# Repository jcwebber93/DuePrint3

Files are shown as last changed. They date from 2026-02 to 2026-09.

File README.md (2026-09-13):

# DuePrint3
Duet 3 to Stratasys PDB Interface Board. Used to convert a Stratasys Prodigy series printer (Dimension, uPrint, Fortus 250) to use a modern control board & firmware. This conversion is fully reversable (assuming the printer functions to begin with). Many thanks to AJ Quick and Archeantus (Jeremy) for their past efforts in detailing the electronics of the Dimension/uPrint machines, as well as sharing details on their Duet 2 WiFi conversions.
* https://wiki.cnc.xyz/Stratasys_uPrint_Retrofit
* https://forum.duet3d.com/topic/12647/another-stratasys-uprint-retrofit

[Additional details for this project on the Duet3D forums.](https://forum.duet3d.com/topic/37434/dueprint-with-a-duet-3-6hc-stratasys-dimension-conversion)

DuetPrint3 Block Diagram

IMG_4153(1)

DuePrint3 v2 5 0

At present, the implementation focuses on the Dimension 1200es printers (the implementations linked above focus on the uPrint series, which is quite similar. The electronics are laid out a touch differently, meaning the layout of the new hardware must change, as well where the stepper motor wiring taps in to the existing harness). The Duet 3 Mainboard 6HC, as well as the DP3EXB module (natively running RepRapFirmware/Duet3Expansion) interface with 17 inputs, and 11 outputs.
### Inputs
|Device|RRF Pin Name|Function|Gcode|Dependancy|Note|
|---|---|---|---|---|---|
|6HC HEADER 7|io2.in|PRINT BED TOUCH PR LIM SW|`M558 P5 H5 F1200:200 T18000 A3 C"!io2.in" ; Z probe`||Used for Z probing|
|6HC HEADER 9|io6.in|Z-AXIS EOT|`M574 Z2 S1 P"!io6.in" ; Z EOT to Z endstop on high side`||Remapped as part of Z homing routine|
|6HC HEADER 11|io4.in|Y-AXIS EOT|`M950 J6 C"!io4.in" ; Y EOT (High, Back)`||Used for Y end of travel (high side, back of printer)|
|6HC HEADER 13|io3.in|X-AXIS EOT|`M950 J5 C"!io3.in" ; X EOT (High)`||Used for X end of travel|
|6HC HEADER 15|io0.in|X-AXIS HOME SW|`M574 X1 S1 P"!io0.in" ; X home limit (low side)`||Used for X homing (low side)|
|6HC HEADER 17|io1.in|Y-AXIS HOME SW|`M574 Y1 S1 P"!io1.in" ; Y home limit (low side, front of printer)`||Used for Y homing (low side, front of printer)|
|6HC HEADER 19|io5.in|Z-AXIS HOME SW|`M950 J7 C"!io5.in" ; Z Home`||Remapped as part of Z homing routine|
|6HC HEADER 21|io8.in|POWER I/O|`M950 J11 C"io8.in" ; Power Switch Status`||Front power switch status|
|6HC HEADER 23|io7.in|PRINT HEAD TEMP ALARM|`M950 J9 C"!io7.in" ; Print Head Temp Alarm`||Print head temperature alarm|
|DP3EXB |PA07|CHAMBER TEMP ALARM|`M950 J10 C"124.pa07" ; Chamber Temp Alarm`||Chamber temperature alarm|
|DP3EXB |PA06|HEAD THERMOSTAT STATUS|`M950 J1 C"124.pa06" ; Head Thermostat`||Head thermostat|
|DP3EXB |PA05|DOOR SWITCH|`M950 J2 C"124.pa05" ; Door Status`||Door switch status|
|DP3EXB |PA04|SUPPORT TOGGLE SW|`M950 J3 C"124.pa04" ; T1 Toggle`||T1 (Support) toggle sensor|
|DP3EXB |PB11|MODEL TOGGLE SW|`M950 J4 C"124.pb08" ; T0 toggle`||T0 (Model) toggle sensor|
|6HC HEADER 18&20|temp0&VSSA|CHAMBER THERM|`M308 S0 A"Chamber" P"temp0" Y"linear-analog" F0 B-42 C113 ; Chamber Temp Sensor`||Chamber temperature sensor|
|6HC HEADER 22&24|temp2&VSSA|SUPPORT THERM|`M308 S1 A"Model" P"temp1" Y"linear-analog" F0 B12.5 C328 ; T1 (Support) Temp Sensor`||Tool 1 (Support) temperature sensor|
|6HC HEADER 26&28|temp1&VSSA|MODEL THERM|`M308 S2 A"Support" P"temp2" Y"linear-analog" F0 B12.5 C328 ; T0 (Model) Temp Sensor`||Tool 0 (Model) temperature sensor|

### Outputs
|Device|RRF Pin Name|Function|Gcode|Dependancy|Note|
|---|---|---|---|---|---|
|6HC HEADER 2|io0.out|120V ON|`M950 P5 C"io0.out" ; 120V On`|Outputs need to be enabled via "M42 P7 S0"|Enables 120V power supplies|
|6HC HEADER 3|out4|48V RTN|`M950 P7 C"!out4"  ; Disable Outputs`||This provides power to DuePrint3 level shifters.|
|6HC HEADER 4|io1.out|POWER ON|`M950 P6 C"io1.out" ; Controlled Shutdown`|Outputs need to be enabled via "M42 P7 S0"|When enabled, allows the printer to handle a controlled shutdown when front power switch is toggled|
|6HC HEADER 6|io3.out|MOTOR ENA|`M950 P1 C"io3.out" ;Extruder Motor`|Outputs need to be enabled via "M42 P7 S0"|Enables the extruder motor|
|6HC HEADER 8|io4.out|CHAMBER HEATER ENA|`M950 H0 C"io4.out" T0 ; Chamber heater, Sensor 0`|Outputs need to be enabled via "M42 P7 S0"|Chamber heater|
|6HC HEADER 10|io2.out|BLOWER ENA|`M950 P0 C"io2.out" ; Head Blower Fan`|Outputs need to be enabled via "M42 P7 S0"|Used to enable or disable head blower fan|
|6HC HEADER 12|io7.out|SUPPORT HEATER ENA|`M950 H2 C"io7.out" T2 ; T1 heater, Sensor 2`|Outputs need to be enabled via "M42 P7 S0"|Tool 1 (Support) heater|
|6HC HEADER 14|io5.out|EXTRUDER MODEL HEATER ENA|`M950 H1 C"io5.out" T1 ; T0 heater, Sensor 1`|Outputs need to be enabled via "M42 P7 S0"|Tool 0 (Model) heater|
|6HC HEADER 16|io6.out|DOOR SOLENOID ENA|`M950 P3 C"io6.out" ; Door Lock`|Outputs need to be enabled via "M42 P7 S0"|Used to enable or disable the door lock|
|DP3EXB |PA08|LED LIGHTS ENA|`M950 P4 C"124.pa24" ; Chamber Lights`||Used to enable or disable chamber lights|
|DP3EXB |PA10|PRINT BED TOUCH PR ENA|`M950 P2 C"124.pa25" ;Doesn't seem to function?`||Does not seem to have a function|

### Other
|Header Pin|Desc.|Label|
|---|---|---|
|6HC HEADER 1|N/A|NC|
|6HC HEADER 5|N/A|48V|
|6HC HEADER 25|N/A|NC|
|6HC HEADER 27|N/A|5V|
|6HC HEADER 29|N/A|GND|
|6HC HEADER 30|N/A|GND|

### Spares Header
|Header Pin|Desc.|Label|
|---|---|---|
|SPARE 1||GND|
|SPARE 2|PA27|SPR4|
|SPARE 3|PA02|SPR1|
|SPARE 4|PA23|SPR3|
|SPARE 5|PA01|SPR2|
|SPARE 6|PA19|I_SPR2|
|SPARE 7|PA12|I_SPR1|
|SPARE 8|PA17|SPR5|
|SPARE 9||5V|
|SPARE 10|PA09|SPR6|
|SPARE 11||GND|
|SPARE 12|PA11|SPR7|
|SPARE 13||12V|
|SPARE 14|PA18|SPR8|

The 6HC directly drives the X, Y, and Z stepper motors (vs. controlling them through the Stratasys PDB). The 6HC, unlike the Duet2 (and Duex boards) does not natively have STEP/DIR pins used to emit step and direction pulses. Instead, a DP3EXB expansion board running a fork of Duet3Expansion is used to natively control the extruder's closed loop DC motor. The extruder can be tuned via the ClosedLoopTuning plugin for DWC, with the motor parameters being configured in Config.g. RRF is able to monitor the motor for position errors.

## Materials
[A detailed BOM can be found here](https://github.com/jcwebber93/DuePrint3/blob/v2.5.0/DuePrint3%20BOM.xlsx), with the approximate cost being ~$660 (60% of this is Duet3D 6HC, DP3EXB Module, and DuetScreen).

## Interface Board Design
[The KidCad project for the DuePrint3 board can be found here](https://github.com/jcwebber93/DuePrint3/tree/v2.5.0/DuePrint3%20KiCad%20Project)

## Wiring
[A detailed wire list can be found here.](https://github.com/jcwebber93/DuePrint3/blob/v2.5.0/DuePrint3%20Wire%20List.xlsx) Connectors & crimps for the Duet 3 6HC are supplied with the board, but are JST VH (stepper motors) and Molex KK / Wurth WR-WTB (Wurth connectors/contacts are supplied with Duet Boards). The interface board 6HC and spares header are JST PHD, and spare 5v and 12v headers are Molex Micro-3.0 series connectors & crimps. The headers for the PBD ribbon cables are Samtec EHT series headers.

## DP3EXB Prep
DP3EXB prep to detailed

## Interface Board Prep
If the Interface Board (w/Sammy-C21) is the only CAN-FD device, aside from the Duet 3 6HC, place a 2-socket jumper on J13 as indicated to enable the CAN-FD termination resistor.



J11 connects to the 6HC. J12 can be used with additional expansion boards (such as a Duet 3 SZP on the print head, which could be used as an accelerometer or for bed scanning), provided the CAN-FD bus is terminated on the additional board.

## RepRapFirmware Prep
At present, the 6HC and DP3EXB are running a fork of 3.6.3 (to be documented). [Configuration files are located here](https://github.com/jcwebber93/DuePrint3/tree/v2.0.0/Duet%203%20Configuration/System%20Directory), and [Macros are located here.](https://github.com/jcwebber93/DuePrint3/tree/v2.0.0/Duet%203%20Configuration/Macros%20Directory)

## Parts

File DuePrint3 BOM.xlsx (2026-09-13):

 |  |  |  |  | $661.01 |  | https://www.digikey.com/short/q54m7hm0
Item | Part Number | Description | Quantity | REF | Price | EXT Price | Note | Link
1 |  | Duet 3 Mainboard 6HC | 1 |  | $269.99 | $269.99 |  | https://www.filastruder.com/collections/duet3d/products/duet-3-mainboard-6hc
2 |  | DuePrint3 v2.5.0 PCB | 1 |  | $30.00 | $30.00
3 | LRS-75-48 | Power Suppy, AC/DC, 48V 75W | 1 |  | $14.10 | $14.10 |  | https://www.digikey.com/en/products/detail/mean-well-usa-inc/LRS-75-48/7705054
4 | PAAD04010BH-0000 | Fan, 5V, 40x10, 0.25A | 2 | FAN 1, FAN 2 | $5.33 | $10.66 | The Stratasys 12V/5V PSU requires a minimum load of 0.7A on 5V, so a "dummy" load is required (else the machine fails to power on). Fans helps fill that "dummy" load. | https://www.digikey.com/en/products/detail/boyd-laconia-llc/PAAD04010BH-0000/20532210
5 | CL21B103KAANNNC | 10nF, 25V X7R Cap, 0805 | 1 | C3 | $0.10 | $0.10 |  | https://www.digikey.com/en/products/detail/samsung-electro-mechanics/CL21B103KAANNNC/3888092
6 | CL21B104KCFSFNE | 0.1 uF, 100V X7R Cap, 0805 | 2 | C1,C2 | $0.10 | $0.20 |  | https://www.digikey.com/en/products/detail/samsung-electro-mechanics/cl21b104kcfsfne/3888581
7 | 150080BS75000 | LED, Blue, 0805 | 1 | D1 (12V) | $0.19 | $0.19 |  | https://www.digikey.com/en/products/detail/w%C3%BCrth-elektronik/150080BS75000/4489912
8 | 150080VS75000 | LED, Green, 0805 | 1 | D2 (5V_SW) | $0.19 | $0.19 |  | https://www.digikey.com/en/products/detail/w%C3%BCrth-elektronik/150080VS75000/4489924
9 | 150080AS75000 | LED, Amber, 0805 | 1 | D3 (5V) | $0.25 | $0.25 |  | https://www.digikey.com/en/products/detail/w%C3%BCrth-elektronik/150080AS75000/11479384
10 | EHT-110-01-F-D | Conn, Header, 20 pos, EHT | 1 | J1 | $2.77 | $2.77 |  | https://www.digikey.com/en/products/detail/samtec-inc/EHT-110-01-F-D/6678014
11 | 436500315 | Conn, Header, 3 pos, MicroFit- 3.0 | 1 | J4 | $1.15 | $1.15 |  | https://www.digikey.com/en/products/detail/molex/0436500315/283462
12 | B14B-PHDSS | Conn, Header, 14 pos, JST PHD, 2.0 | 1 | J14 | $0.47 | $0.47 |  | https://www.digikey.com/en/products/category/rectangular-connectors/2027
13 | B30B-PHDSS | Conn, Header, 30 pos, JST PHD, 2.0 | 1 | J16 | $0.86 | $0.86 |  | https://www.digikey.com/en/products/detail/jst-sales-america-inc/B30B-PHDSS/926678
14 | SS-6466S-A-PG1 | Conn, 6p6c R/A, RJ11 | 2 | J11,J12 | $0.61 | $1.22 |  | https://www.digikey.com/en/products/detail/stewart-connector/SS-6466S-A-PG1/1642347
15 | 61300311121 | Conn, Header, 3 pos | 2 | J13,J15 | $0.13 | $0.26 | Can buy larger and cut down | https://www.digikey.com/en/products/detail/w%C3%BCrth-elektronik/61300311121/4846825
16 | EHT-125-01-F-D | Conn, Header, 50 pos, EHT | 2 | J2,J5 | $6.91 | $13.82 |  | https://www.digikey.com/en/products/detail/samtec-inc/EHT-125-01-F-D/6694880
17 | 436500215 | Conn, Header, 2 pos, MicroFit- 3.0 | 4 | J3,J6,J8,J9 | $0.89 | $3.56 |  | https://www.digikey.com/en/products/detail/molex/0436500215/283461
18 | 61301611821 | Conn, Header, 16 pos | 2 | J90,J91 | $0.61 | $1.22 |  | https://www.digikey.com/en/products/detail/w%C3%BCrth-elektronik/61301611821/6137797
19 | QPC02SXGN-RC | Jumper, Shorting, 2 Pos | 2 | J92,J93 | $0.10 | $0.20 | For CAN-FD termination and Motor En select | https://www.digikey.com/en/products/detail/sullins-connector-solutions/QPC02SXGN-RC/2618262
20 | CRCW08053K74FKEA | 3.74K Res, 1% 0.125W, 0805 | 1 | R1 | $0.10 | $0.10 |  | https://www.digikey.com/en/products/detail/vishay-dale/crcw08053k74fkea/1175701
21 | CRCW080531K6FKEA | 31.6K Res, 1% 0.125W, 0805 | 1 | R2 | $0.10 | $0.10 |  | https://www.digikey.com/en/products/detail/vishay-dale/CRCW080531K6FKEA/1175806
22 | ERJ-6ENF1003V | 100K Res, 1% 0.125W, 0805 | 1 | R9 | $0.10 | $0.10 |  | https://www.digikey.com/en/products/detail/panasonic-industry/erj-6enf1003v/111841
23 | CRCW0805120RFKEA | 120 Res, 0805 | 1 | R16 | $0.10 | $0.10 |  | https://www.digikey.com/en/products/detail/vishay-dale/CRCW08051K00FKEA/1175637
24 | CRCW080510K0FKEA | 10K Res, 1% 0.25W, 0805 | 8 | R10,R11,R12,R13,R14,R15,R17,R18 | $0.10 | $0.80 |  | https://www.digikey.com/en/products/detail/vishay-dale/crcw080510k0fkea/1175751
25 | CRCW08052K20FKEA | 2K2 | 2 | R19,R20 | $0.10 | $0.20 |  | https://www.digikey.com/en/products/detail/vishay-dale/CRCW08052K20FKEA/1175673
26 | CRCW08052K00FKEA | 2K Res, 1% 0.125W, 0805 | 3 | R3,R4,R6 | $0.10 | $0.30 |  | https://www.digikey.com/en/products/detail/vishay-dale/CRCW08052K00FKEA/1175669
27 | CRCW08051K00FKEA | 1K Res, 1% 0.125W, 0805 | 3 | R5,R7,R8 | $0.10 | $0.30 |  | https://www.digikey.com/en/products/detail/vishay-dale/CRCW08051K00FKEA/1175637
28 | DP3EXB | DP3EXB | 1 | U4 | $40.00 | $40.00 | MCU Module | https://github.com/jcwebber93/DP3EXB
29 | SN74AHCT125DR | SN74AHCT125DR, 14-SOIC | 2 | U1,U2 | $0.40 | $0.80 |  | https://www.digikey.com/en/products/detail/texas-instruments/SN74AHCT125DR/376412
30 | 39012086 | Conn, Plug, 8 pos, Mini-Fit Jr | 1 | P2 | $0.66 | $0.66 |  | https://www.digikey.com/en/products/detail/molex/0039012086/930285
31 | 39012205 | Conn, Rcpt, 20 pos, Mini-Fit Jr | 1 | P3 | $1.48 | $1.48 |  | https://www.digikey.com/en/products/detail/molex/0039012205/930279
32 | 39012206 | Conn, Plug, 20 pos, Mini-Fit Jr | 1 | P1 | $1.20 | $1.20 |  | https://www.digikey.com/en/products/detail/molex/0039012206/4693014
33 | 39000048 | Pin, 22-28 AWG, Mini-Fit Jr | 18 |  | $0.06 | $1.10 |  | https://www.digikey.com/en/products/detail/molex/0039000048/1643437
34 | 39000046 | Socket, 22-28 AWG, Mini-Fit Jr | 6 |  | $0.05 | $0.31 |  | https://www.digikey.com/en/products/detail/molex/0039000046/1643436
35 | 430300010 | Socket, 26-30 AWG, Micro-Fit 3.0 | 4 |  | $0.20 | $0.80 |  | https://www.digikey.com/en/products/detail/molex/0430300010/252480
36 | 436450200 | Conn, Rcpt, 2 pos, Micro-Fit 3.0 | 2 | P8, P9 | $0.39 | $0.78 |  | https://www.digikey.com/en/products/detail/molex/0436450200/268974
37 | PHDR-30VS | Conn, Rcpt, 30 pos, JST PHD, 2.0 | 1 | P7 | $0.48 | $0.48 |  | https://www.digikey.com/en/products/detail/jst-sales-america-inc/PHDR-30VS/608621
38 | PHDR-14VS | Conn, Rcpt, 14 pos, JST PHD, 2.0 | 1 | Spares Header | $1.07 | $1.07 |  | https://www.digikey.com/en/products/detail/molex/0430251800/531407
39 | SPHD-002T-P0.5 | Socket, 24-28 AWG, JST SPHD | 27 |  | $0.02 | $0.57 |  | https://www.digikey.com/en/products/detail/jst-sales-america-inc/SPHD-002T-P0-5/608754
40 | VHR-4N | Conn, Rcpt, 4 pos, JST VH | 3 | P4,P5,P6 | $0.12 | $0.36 | Included in 6HC purchase | https://www.digikey.com/en/products/detail/jst-sales-america-inc/VHR-4N/608626
41 | SVH-21T-P1.1 | Socket, 18-22 AWG, JST VH | 12 |  | $0.12 | $1.44 | Included in 6HC purchase | https://www.mouser.com/ProductDetail/JST-Commercial/SVH-21T-P11?qs=QpmGXVUTftHffPDBVqr85w%3D%3D
42 | 61900511621 | Conn, Rcpt, 5 pos, WR-WTB | 9 | IO_0 IO_1 IO_2 IO_3 IO_4 IO_5 IO_6 IO_7 IO_8 | $0.17 | $1.53 | Included in 6HC purchase | https://www.digikey.com/en/products/detail/w%C3%BCrth-elektronik/61900511621/2508639
43 | 61900211621 | Conn, Rcpt, 2 pos, WR-WTB | 3 | TEMP0 TEMP1 TEMP2 | $0.13 | $0.39 | Included in 6HC purchase | https://www.digikey.com/en/products/detail/w%C3%BCrth-elektronik/61900211621/2508636
44 | 61900411621 | Conn, Rcpt, 4 pos, WR-WTB | 1 | OUT4 | $0.17 | $0.17 | Included in 6HC purchase | https://www.digikey.com/en/products/detail/w%C3%BCrth-elektronik/61900411621/2508638
45 | 61900113722DEC | Socket, 22-28 AWG, WR-WTB | 28 |  | $0.15 | $4.20 | Included in 6HC purchase | https://www.digikey.com/en/products/detail/w%C3%BCrth-elektronik/61900113722DEC/2508640
46 | 350570-1 | Socket, 18-24 AWG, MATE-N-LOK | 6 |  | $0.07 | $0.40 |  | https://www.digikey.com/en/products/detail/te-connectivity-amp-connectors/350570-1/287662
47 | 350536-1 | Socket, 14-20 AWG, MATE-N-LOK | 3 |  | $0.06 | $0.18 |  | https://www.digikey.com/en/products/detail/te-connectivity-amp-connectors/350536-1/287712
48 | 350218-1 | Pin, 14-20 AWG, MATE-N-LOK | 6 |  | $0.06 | $0.35 |  | https://www.digikey.com/en/products/detail/te-connectivity-amp-connectors/350218-1/287751
49 | 350561-1 | Pin, 18-24 AWG, MATE-N-LOK | 3 |  | $0.06 | $0.18 |  | https://www.digikey.com/en/products/detail/te-connectivity-amp-connectors/350561-1/287669
50 | 350720-1 | Conn, Plug, 9 pos, MATE-N-LOK | 1 | P10 | $0.83 | $0.83 |  | https://www.digikey.com/en/products/detail/te-connectivity-amp-connectors/350720-1/213757
51 | 350782-1 | Conn, Rcpt, 9 pos, MATE-N-LOK | 1 | P11 | $0.51 | $0.51 |  | https://www.digikey.com/en/products/detail/te-connectivity-amp-connectors/350782-1/213758
52 | 130517 | Spade Terminal, 16-22 AWG, M4 | 10 |  | $0.43 | $4.30 | M4 or #8 stud, sized for your wires connecting VAC and VDC to 48VDC and 6HC | https://www.digikey.com/en/products/detail/te-connectivity-amp-connectors/130517/1864399
53 |  | RJ11 connectors |  |  |  | $0.00 | In case custom length/custom purpose CAN-FD cables are desired
54 | 14AWG |  | 13.75 |  | $0.48 | $6.61 | Lengths for cost estimation only
55 | 18AWG |  | 15.25 |  | $0.38 | $5.79 | Lengths for cost estimation only
56 | 28AWG |  | 36.67 |  | $0.32 | $11.84 | Lengths for cost estimation only
57 | 22AWG |  | 72 |  | $0.35 | $25.49 | Lengths for cost estimation only
58 |  | DuetScreen | 1 |  | $123.00 | $123.00 |  | https://www.filastruder.com/collections/electronics/products/duet3d-duetscreen
59 |  | 10ft USB-C Cable | 1 |  | $9.99 | $9.99 | Duet 6HC <-> DuetScreen, cable needs to support data | https://www.amazon.com/dp/B08PVPTNZL?th=1
60 |  | Interface Plate | 1 |  | $30.00 | $30.00 |  | https://github.com/jcwebber93/DuePrint3/blob/v2.5.0/Interface%20Plate.STEP
61 |  | 48VDC Plate | 1 |  | $15.00 | $15.00 |  | https://github.com/jcwebber93/DuePrint3/blob/v2.5.0/48VDC%20Plate.STEP
62 |  | Fan Bracket | 2 |  | $8.00 | $16.00 |  | https://github.com/jcwebber93/DuePrint3/blob/v2.5.0/Fan%20Bracket.STEP
63 |  |  |  |  |  | $0.00
64 |  |  |  |  |  | $0.00
65

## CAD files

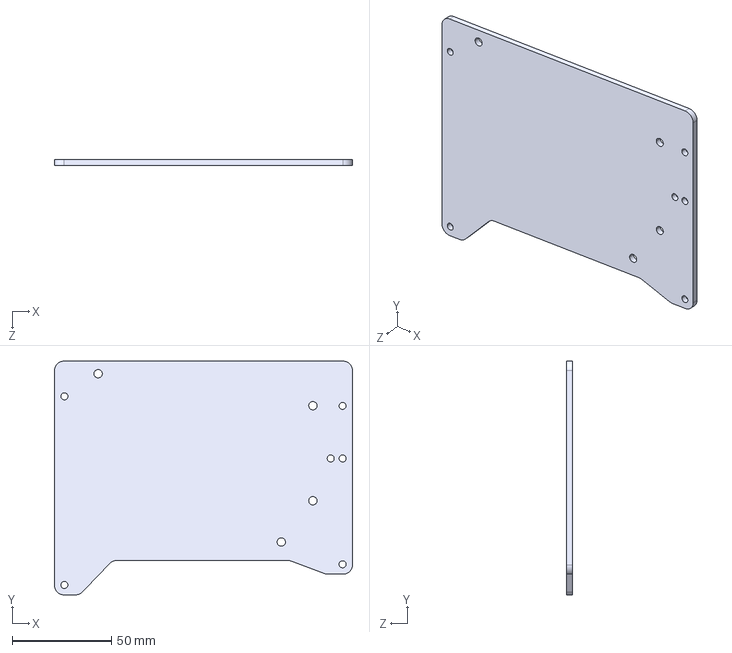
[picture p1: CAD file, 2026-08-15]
48VDC Plate.STEP
150.5 x 118.0 x 3.00 mm

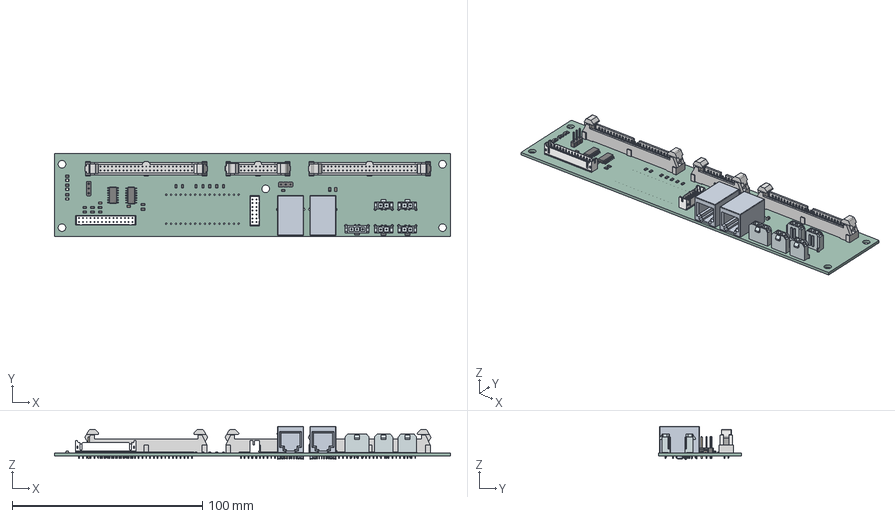
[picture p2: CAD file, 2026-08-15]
DuePrint3 KiCad Project/2.5.0 DuePrint3.step
208.2 x 43.6 x 17.6 mm
LED_0805_2012Metric x 3
R_0805_2012Metric x 20
DP3EXB
C_0805_2012Metric x 3
MF3-1x2-436500215 x 4
C-95-01-25-D- x 2
EHT-First_Position_Indicator x 3
EHT-125-01-D_header x 2
SOIC-14_3.9x8.7mm_P1.27mm x 2
SS-6466S-A-PG1 x 2
MF3-1x3-436500315
BxB-PHDSS_30
pin^BxB-PHDSS ass x 44
BxB-PHDSS_14
C-95-01-10-D-
EHT-110-01-D_header
PinHeader_1x03_P2.54mm_Vertical x 2
DuePrint3_PCB

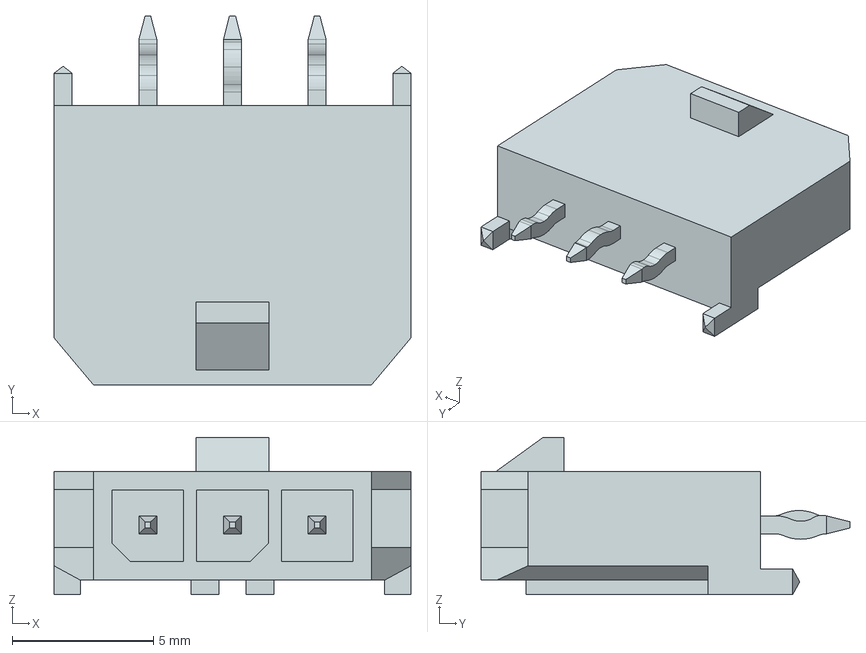
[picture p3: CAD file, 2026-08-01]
DuePrint3 KiCad Project/Components/MF3-1x3-436500315.stp
12.7 x 13.1 x 5.57 mm

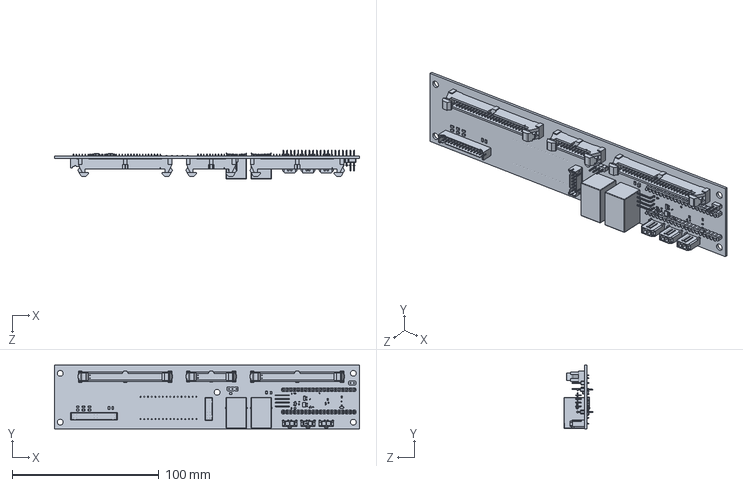
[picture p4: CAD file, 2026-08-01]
DuePrint3 KiCad Project/2.0.0 DuePrint3.step.SLDPRT
208.2 x 43.6 x 19.7 mm

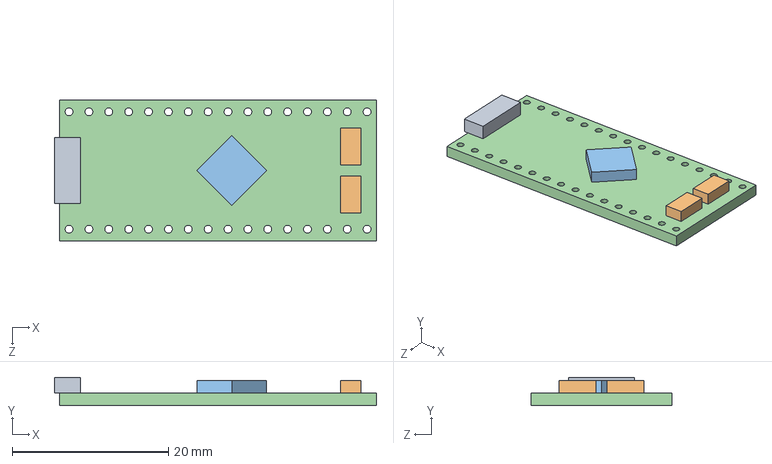
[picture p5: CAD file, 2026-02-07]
DuePrint3 KiCad Project/Components/SAMMY-C21.STEP
41.2 x 3.60 x 18.0 mm

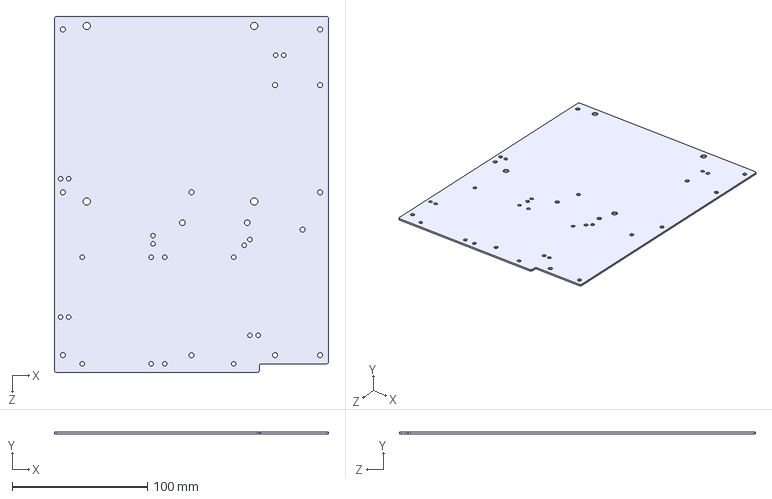
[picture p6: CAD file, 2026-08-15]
Interface Plate.STEP
203.2 x 1.50 x 263.6 mm

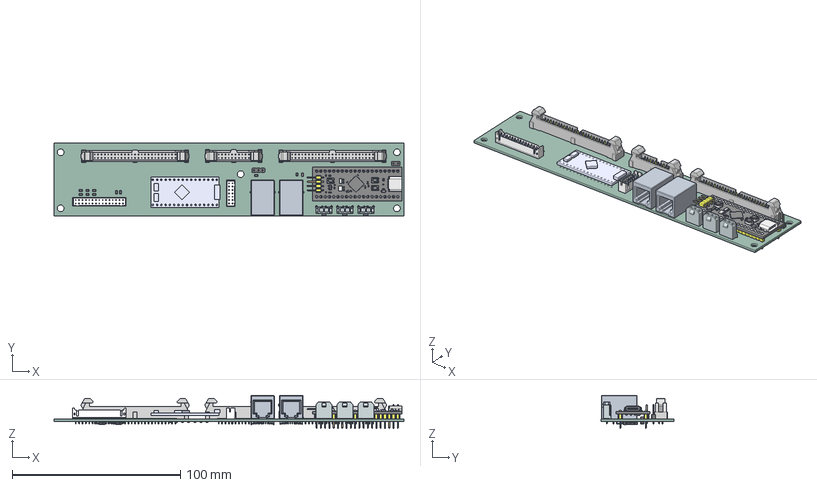
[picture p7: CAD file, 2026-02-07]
DuePrint3 KiCad Project/2.0.0 DuePrint3.step
208.2 x 43.6 x 19.7 mm
SAMMY-C21
R_0805_2012Metric x 17
MF3-1x2-436500215 x 3
C-95-01-25-D- x 2
EHT-First_Position_Indicator x 3
EHT-125-01-D_header x 2
Board_001
STM32F4 Chip_001
Surface Mount Transistor_001
0603 Resistor_001
0603 Capacitor_001
0402 Capacitor_001
0402 Resistor_001
0402 Resistor_002
0402 Resistor_003
0402 Resistor_004
0402 Resistor_005
0402 Resistor_006
0402 Resistor_007
0402 Resistor_008
0402 Capacitor_002
0402 Capacitor_003
0402 Capacitor_004
0402 Capacitor_005
0402 Capacitor_006
0402 Capacitor_007
0402 Capacitor_008
0402 Capacitor_009
0402 Capacitor_010
0402 Capacitor_011
0402 Capacitor_012
0402 Capacitor_013
Diode 2_001
SM LED_001
1x20 Male Header_001
1x20 Male Header_002
Tac Switch_001
Tac Switch_002
Tac Switch_003
USB-C Connector_001
1x4 Right Angle Male Header_001
Crystal 1_001
Crystal 2_001
SS-6466S-A-PG1 x 2
PinHeader_2x01_P2.54mm_Vertical
BxB-PHDSS_30
pin^BxB-PHDSS ass x 44
BxB-PHDSS_14
C-95-01-10-D-
EHT-110-01-D_header
C_0805_2012Metric x 3
PinHeader_1x03_P2.54mm_Vertical
SOIC-14_3.9x8.7mm_P1.27mm x 2
DuePrint3_PCB

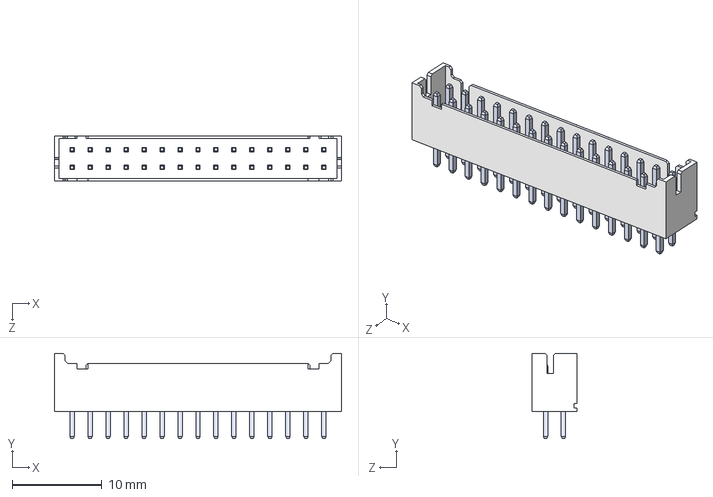
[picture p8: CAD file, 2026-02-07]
DuePrint3 KiCad Project/Components/B30B-PHDSS--3DModel-STEP-56544.STEP
31.9 x 9.50 x 5.00 mm
BxB-PHDSS_30
pin^BxB-PHDSS ass x 30

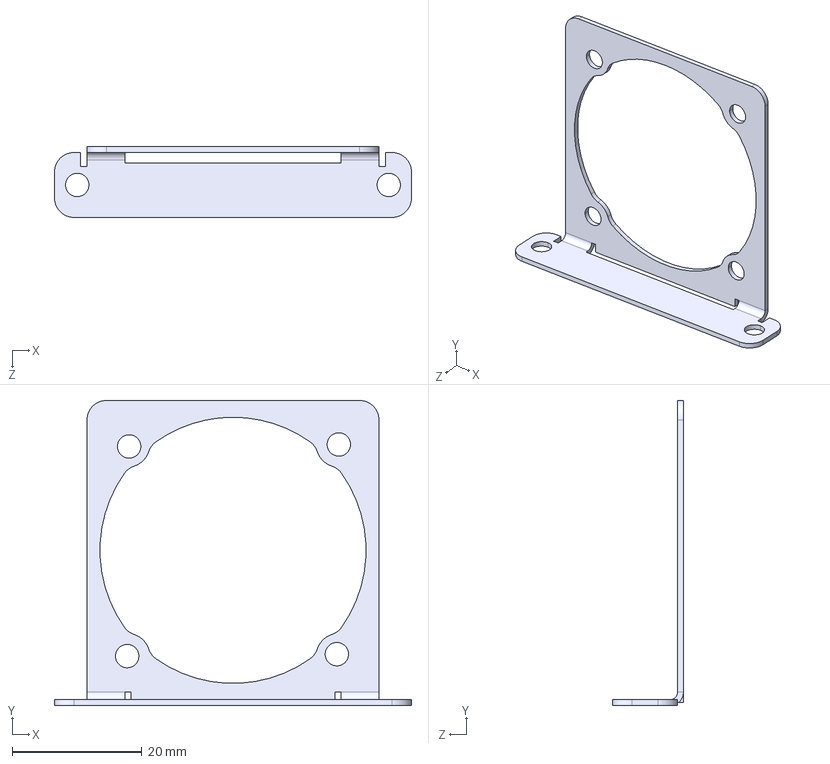
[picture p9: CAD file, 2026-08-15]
Fan Bracket.STEP
55.0 x 47.0 x 10.9 mm

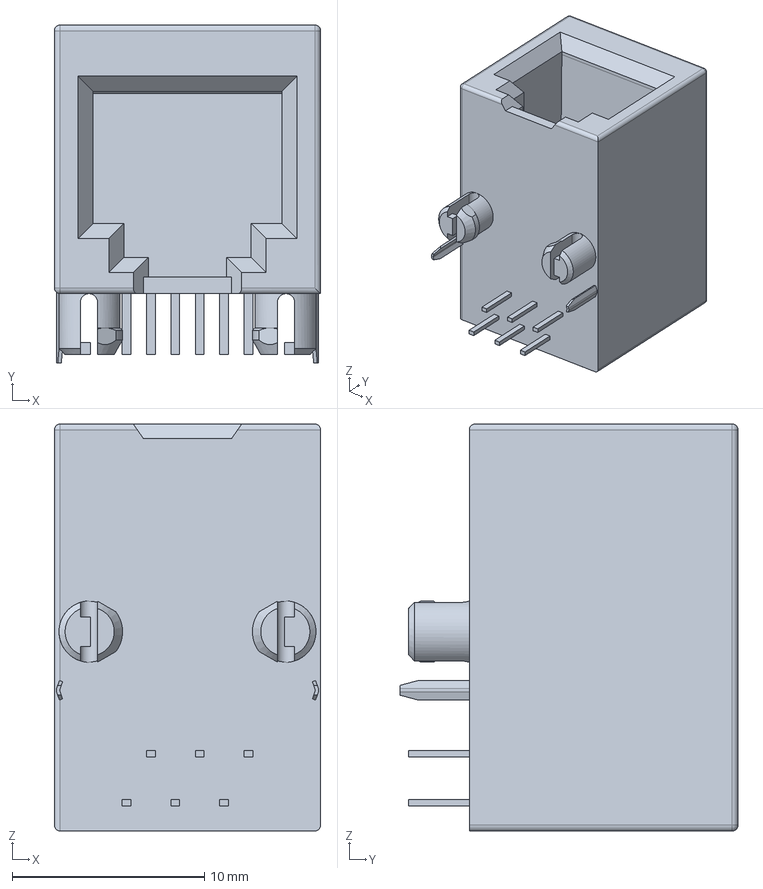
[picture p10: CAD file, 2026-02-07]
DuePrint3 KiCad Project/Components/SS-6466S-A-PG1.stp
13.8 x 17.6 x 21.2 mm

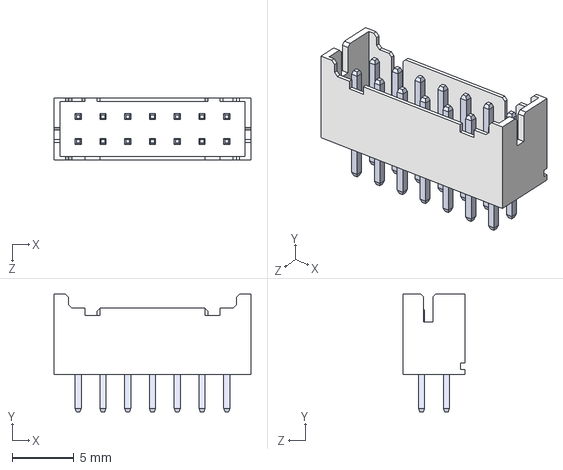
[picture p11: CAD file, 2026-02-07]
DuePrint3 KiCad Project/Components/B14B-PHDSS--3DModel-STEP-56544.STEP
15.9 x 9.50 x 5.00 mm
BxB-PHDSS_14
pin^BxB-PHDSS ass x 14

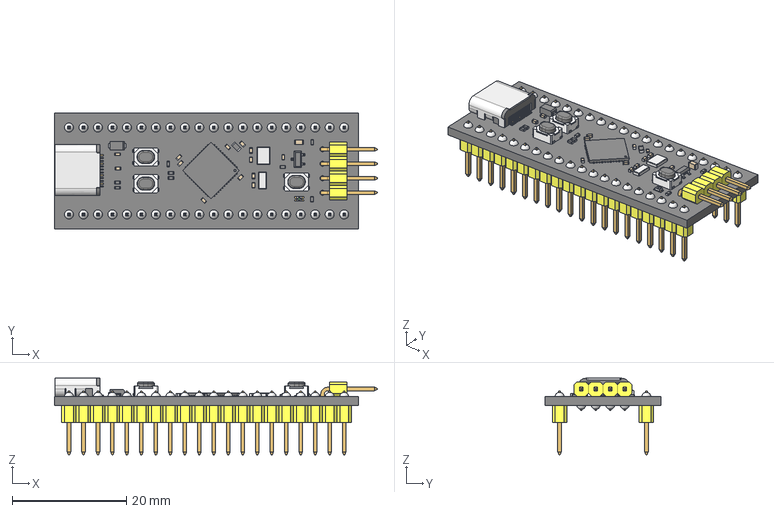
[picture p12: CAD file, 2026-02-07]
DuePrint3 KiCad Project/Components/Black Pill.step
56.6 x 20.3 x 13.4 mm

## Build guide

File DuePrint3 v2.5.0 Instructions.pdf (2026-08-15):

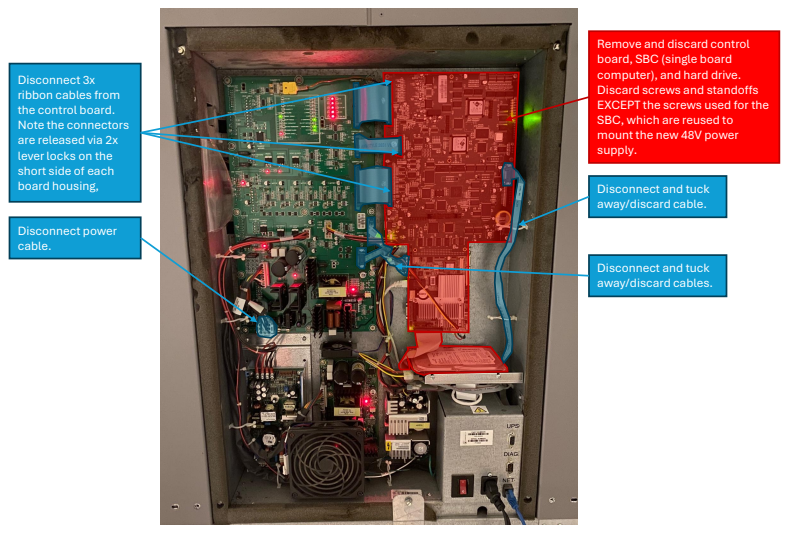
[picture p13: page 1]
Disconnect power cable.

Remove and discard control
board, SBC (single board
computer), and hard drive.
Discard screws and standoffs
EXCEPT the screws used for the
SBC, which are reused to
mount the new 48V power
supply.

Disconnect 3x
ribbon cables from
the control board.
Note the connectors
are released via 2x
lever locks on the
short side of each
board housing,

Disconnect and tuck
away/discard cable.

away/discard cables.

## Duet 6HC Prep

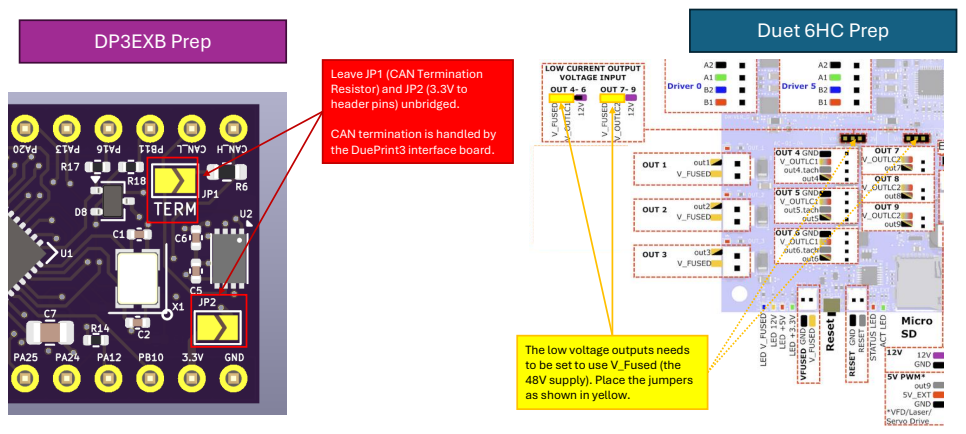
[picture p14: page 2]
DP3EXB Prep

Leave JP1 (CAN Termination
Resistor) and JP2 (3.3V to
header pins) unbridged.

CAN termination is handled by
the DuePrint3 interface board.

The low voltage outputs needs
to be set to use V_Fused (the
48V supply). Place the jumpers
as shown in yellow.

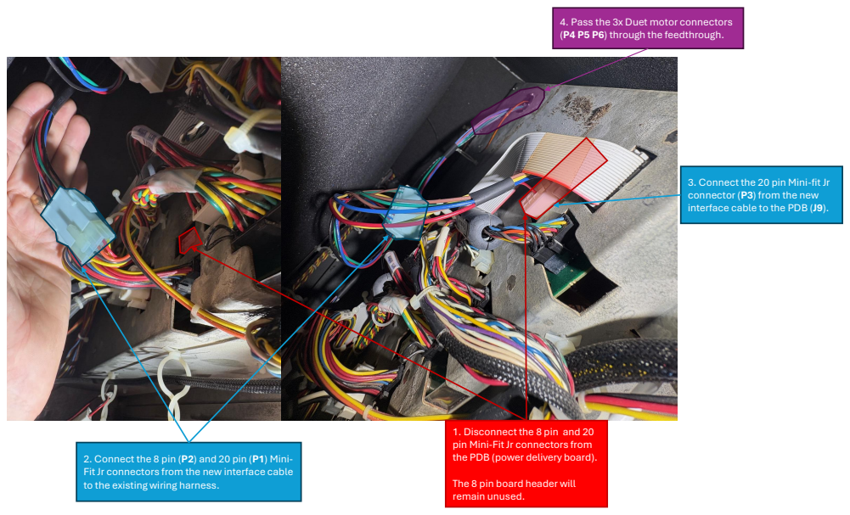
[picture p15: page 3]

4. Pass the 3x Duet motor connectors
(P4 P5 P6) through the feedthrough.

3. Connect the 20 pin Mini-fit Jr
connector (P3) from the new
interface cable to the PDB (J9).

1. Disconnect the 8 pin and 20
pin Mini-Fit Jr connectors from
the PDB (power delivery board).

2. Connect the 8 pin (P2) and 20 pin (P1) Mini-
Fit Jr connectors from the new interface cable
to the existing wiring harness.

The 8 pin board header will
remain unused.

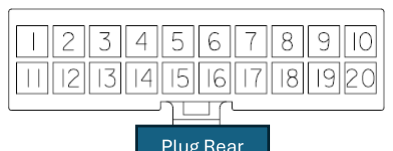
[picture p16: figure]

Plug Rear

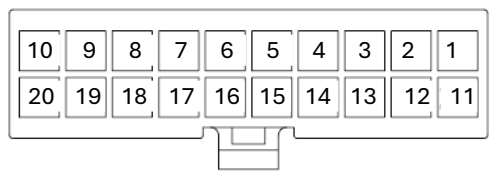
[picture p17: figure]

Recpt. Rear

P2 | P3 | P1

### Y Motor

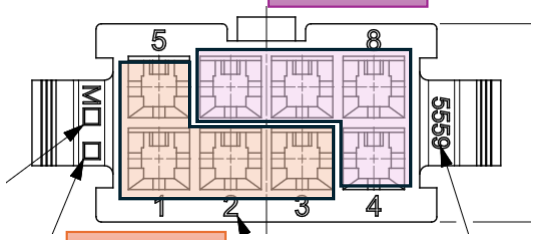
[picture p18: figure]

### Z Motor

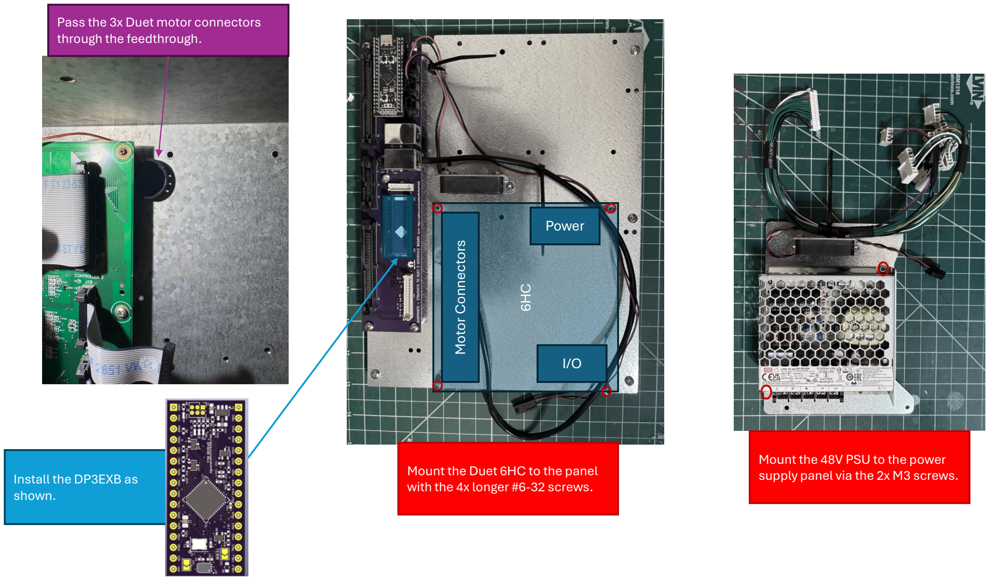
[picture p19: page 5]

6HC

Pass the 3x Duet motor connectors through the feedthrough.

Motor Connectors

Power

I/O

Mount the Duet 6HC to the panel with the 4x longer #6-32 screws.

Mount the 48V PSU to the power supply panel via the 2x M3 screws. Install the DP3EXB as shown.

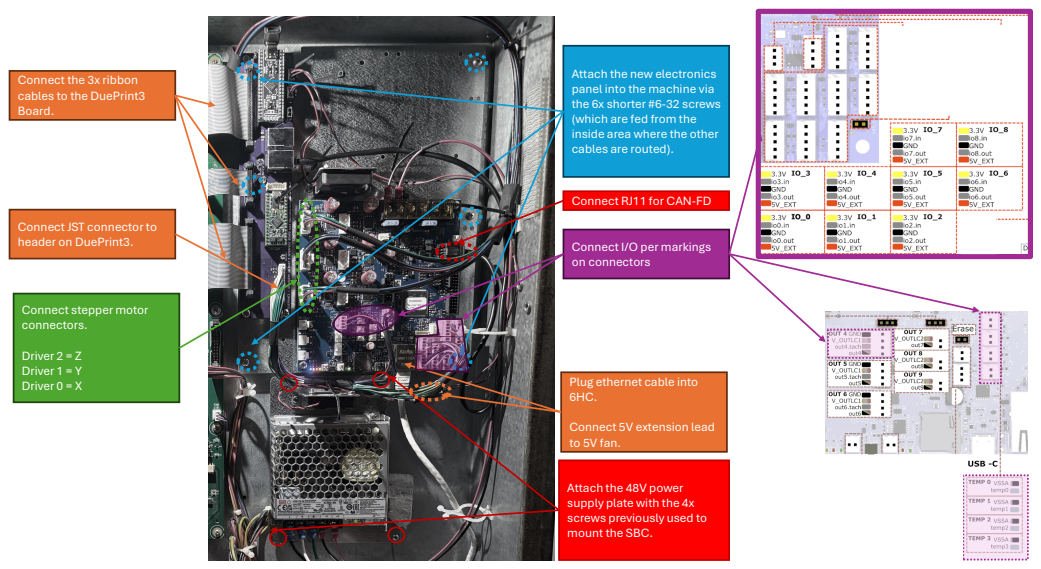
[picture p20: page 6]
-32 screws; Driver 2 = Z Driver 1 = Y Driver 0 = X

Attach the new electronics
panel into the machine via
the 6x shorter #6
(which are fed from the
inside area where the other
cables are routed).

Connect the 3x ribbon
cables to the DuePrint3
Board.

Connect RJ11 for CAN

Connect JST connector to
header on DuePrint3.

Connect I/O per markings
on connectors

Connect stepper motor
connectors.

Plug ethernet cable into

Connect 5V extension lead
to 5V fan.

Attach the 48V power
supply plate with the 4x
screws previously used to
mount the SBC.

## Additional images of connected Duet 6HC

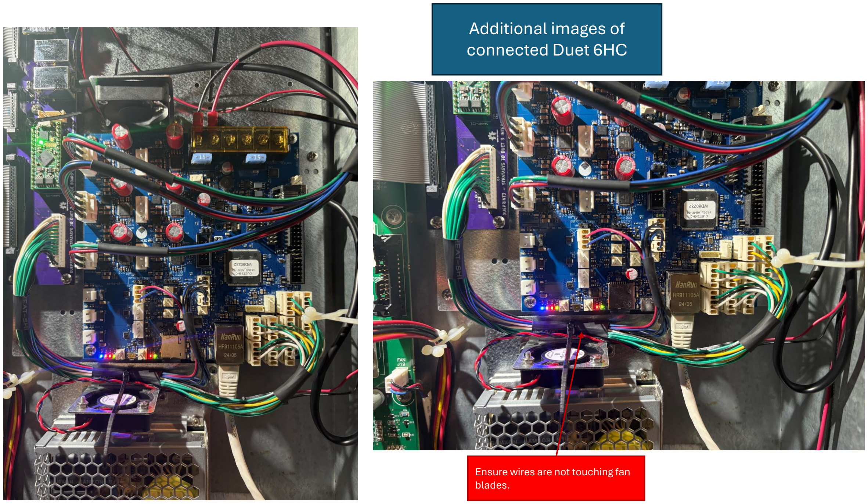
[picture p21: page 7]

Ensure wires are not touching fan blades.

1

2 3

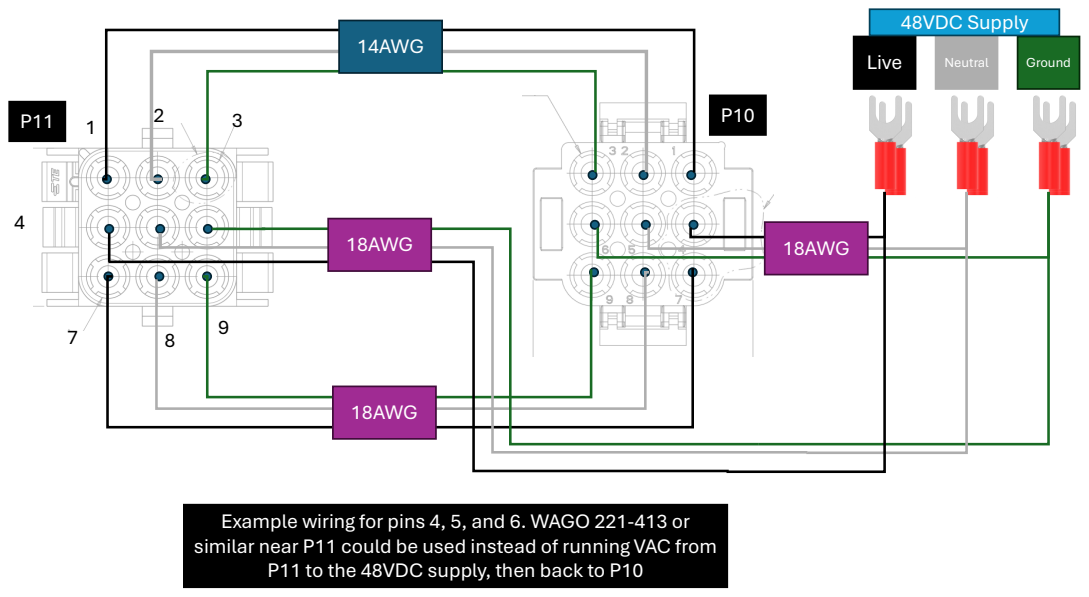
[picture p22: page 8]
14AWG; 18AWG; Live; Neutral; Ground; 48VDC Supply

Example wiring for pins 4, 5, and 6. WAGO 221-413 or
similar near P11 could be used instead of running VAC from
P11 to the 48VDC supply, then back to P10

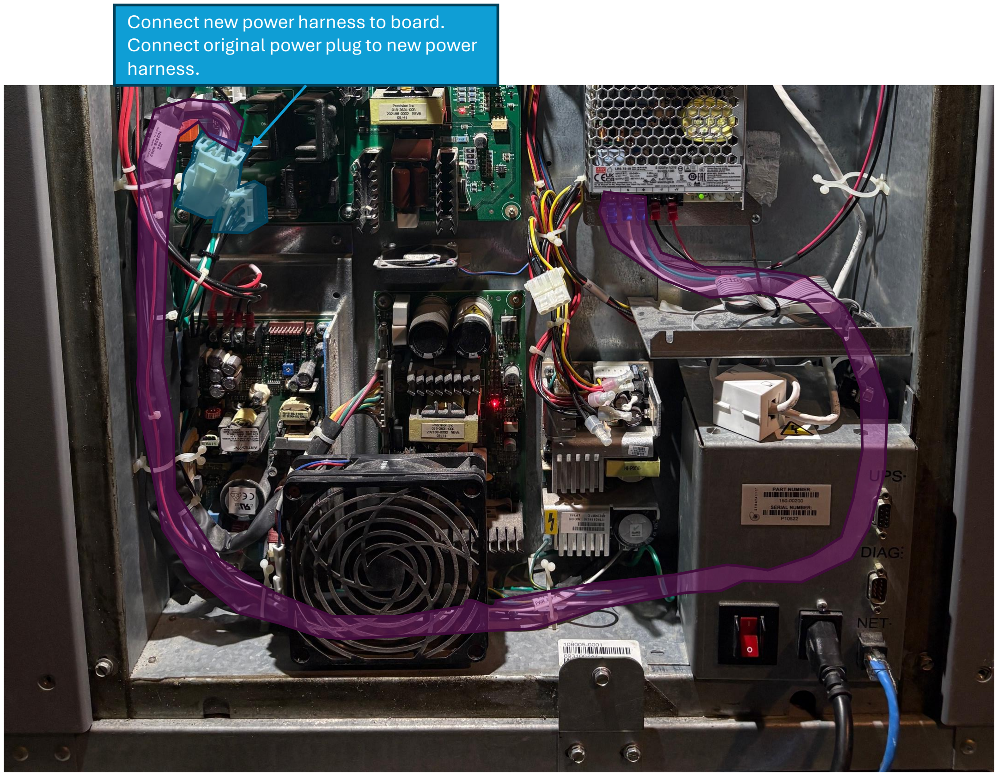
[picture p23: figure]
Connect new power harness to board.; harness.

Connect original power plug to new power

Route power leads approximately as shown. You may wish to temporarily remove the power inlet module, which is retained by 3x screws.

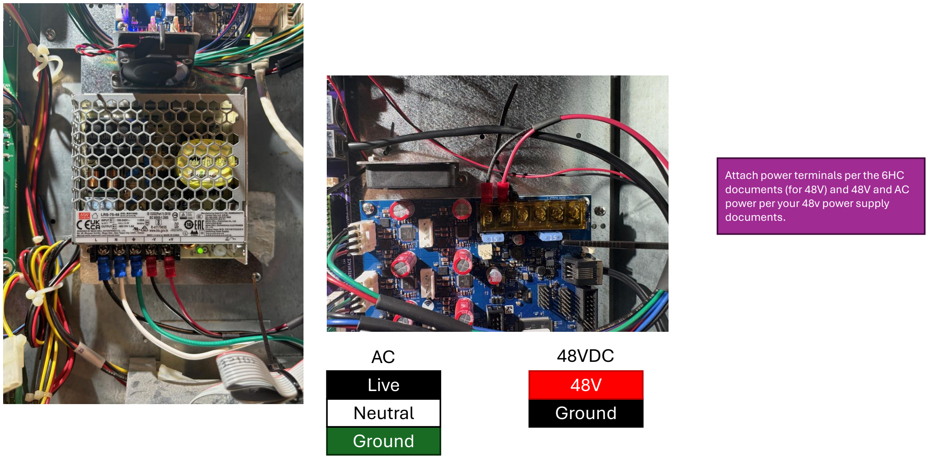
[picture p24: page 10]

Attach power terminals per the 6HC documents (for 48V) and 48V and AC power per your 48v power supply documents.

## Ground

## Neutral

## Live Ground

48V

AC | 48VDC

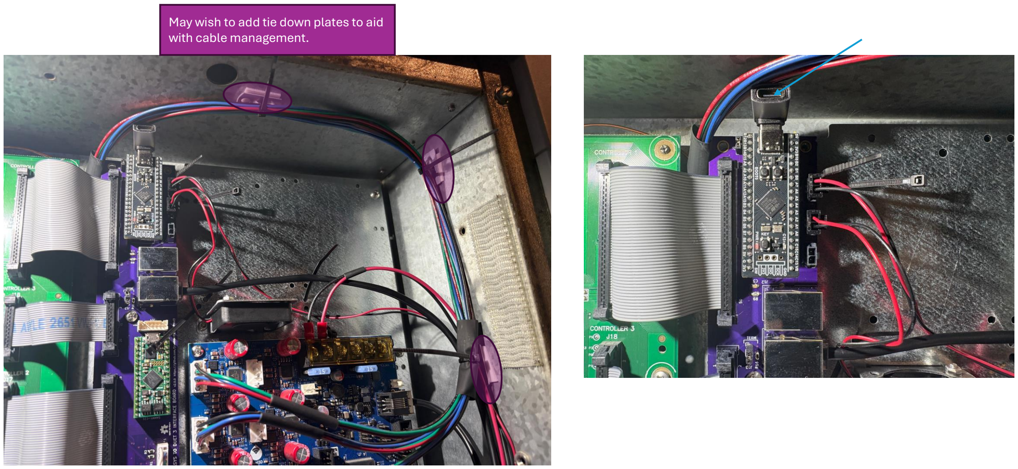
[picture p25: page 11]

May wish to add tie down plates to aid with cable management.

## Studs on Front Side Nuts on Back Side

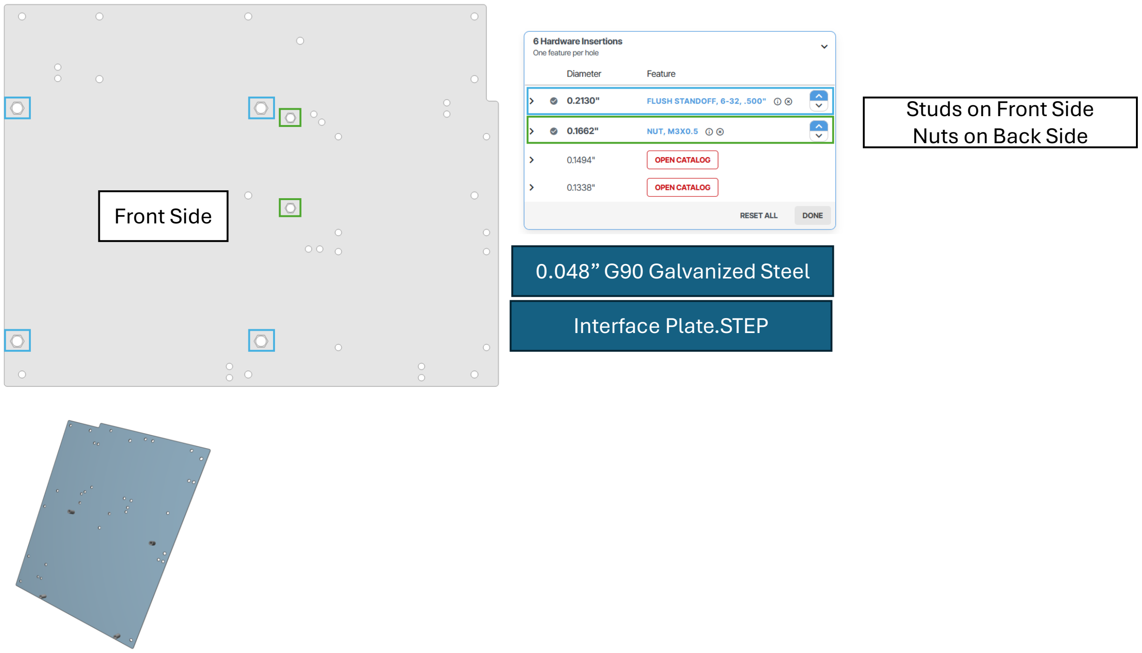
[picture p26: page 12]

## 0.048” G90 Galvanized Steel

## Interface Plate.STEP

## Front Side

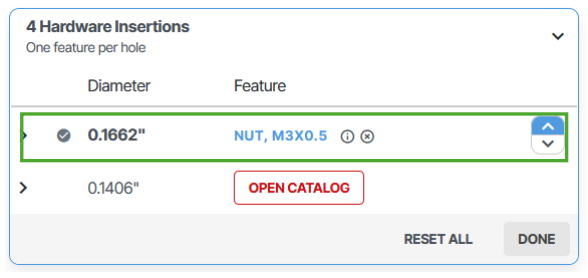
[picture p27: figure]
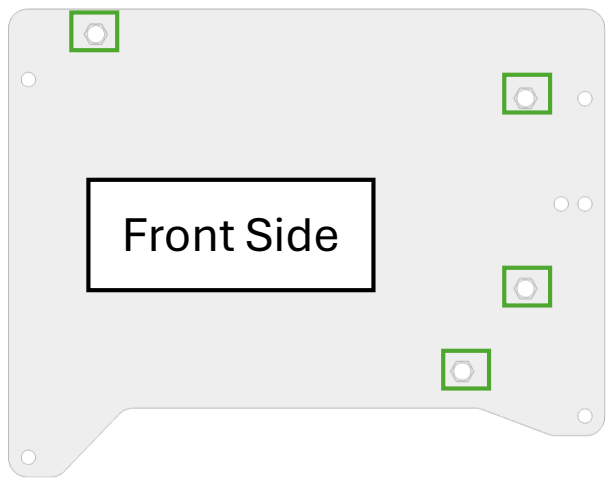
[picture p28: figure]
Front Side

## 0.048” G90 Galvanized Steel

## 48VDC Plate.STEP

## Nuts on Back Side

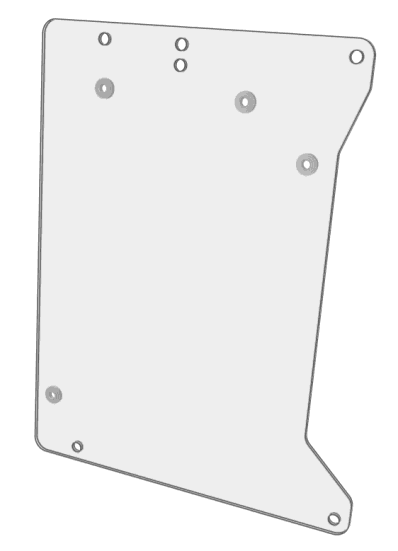
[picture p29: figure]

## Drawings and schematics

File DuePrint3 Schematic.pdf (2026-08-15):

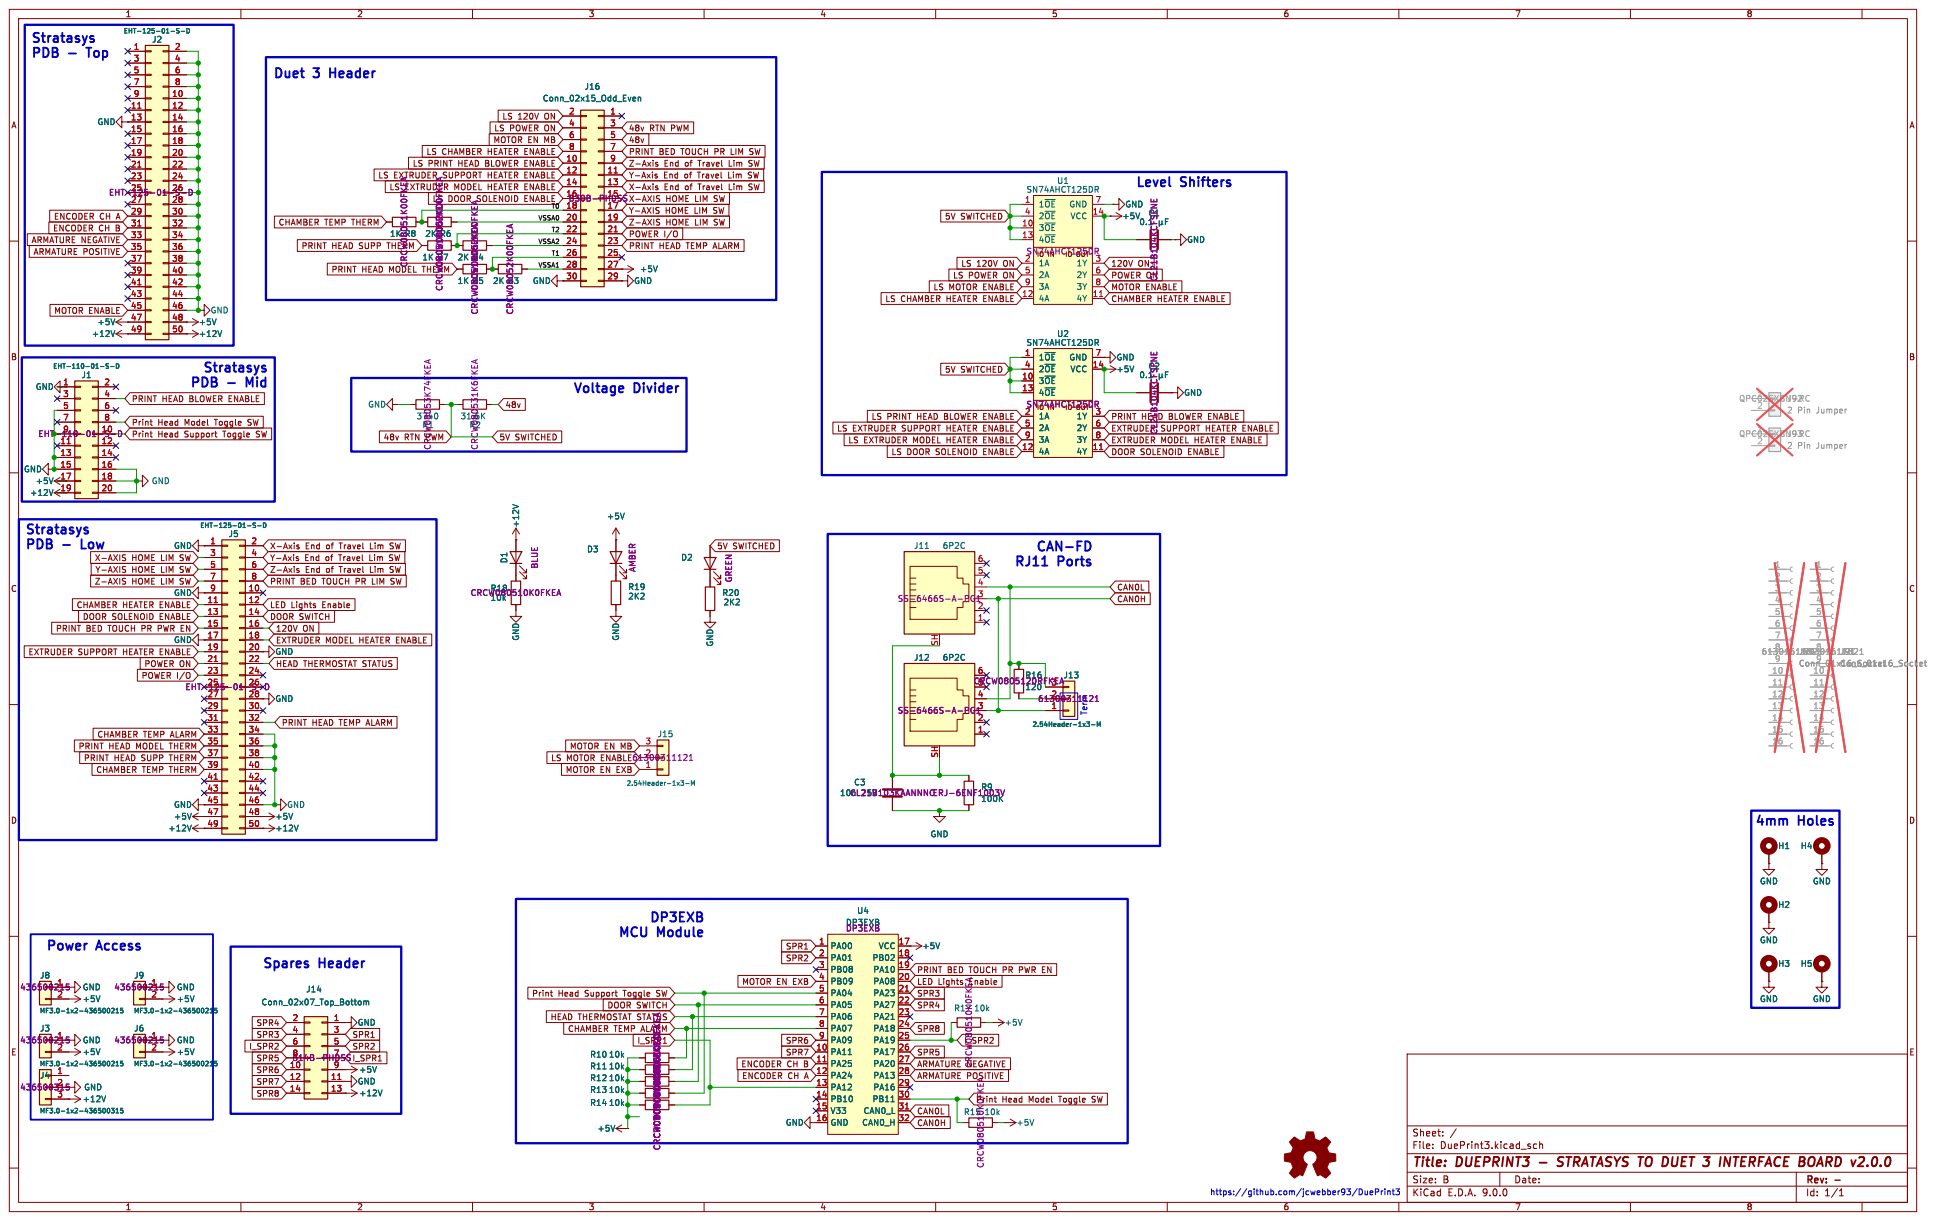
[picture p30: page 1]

LS CHAMBER HEATER ENABLE
LS PRINT HEAD BLOWER ENABLE

LS EXTRUDER SUPPORT HEATER ENABLE
LS EXTRUDER MODEL HEATER ENABLE

LS DOOR SOLENOID ENABLE

ENCODER CH A MOTOR ENABLE
ENCODER CH B
ARMATURE POSITIVE

PRINT HEAD SUPP THERM

PRINT HEAD MODEL THERM

EXTRUDER MODEL HEATER ENABLE DOOR SOLENOID ENABLE CHAMBER HEATER ENABLE

PRINT HEAD BLOWER ENABLE
EXTRUDER SUPPORT HEATER ENABLE

X-AXIS HOME LIM SW
Y-AXIS HOME LIM SW
Z-AXIS HOME LIM SW

CHAMBER HEATER ENABLE
DOOR SOLENOID ENABLE
PRINT BED TOUCH PR PWR EN

PRINT HEAD TEMP ALARM

CHAMBER TEMP ALARM
CHAMBER TEMP THERM

MOTOR EN MB MOTOR EN EXB
LS MOTOR ENABLE

LED Lights Enable ARMATURE POSITIVE
SPR4 SPR3 SPR8 CAN0L

Print Head Support Toggle SW
HEAD THERMOSTAT STATUS DOOR SWITCH

Print Head Model Toggle SW

Id: 1/1 Title: DUEPRINT3 - STRATASYS TO DUET 3 INTERFACE BOARD v2.0.0

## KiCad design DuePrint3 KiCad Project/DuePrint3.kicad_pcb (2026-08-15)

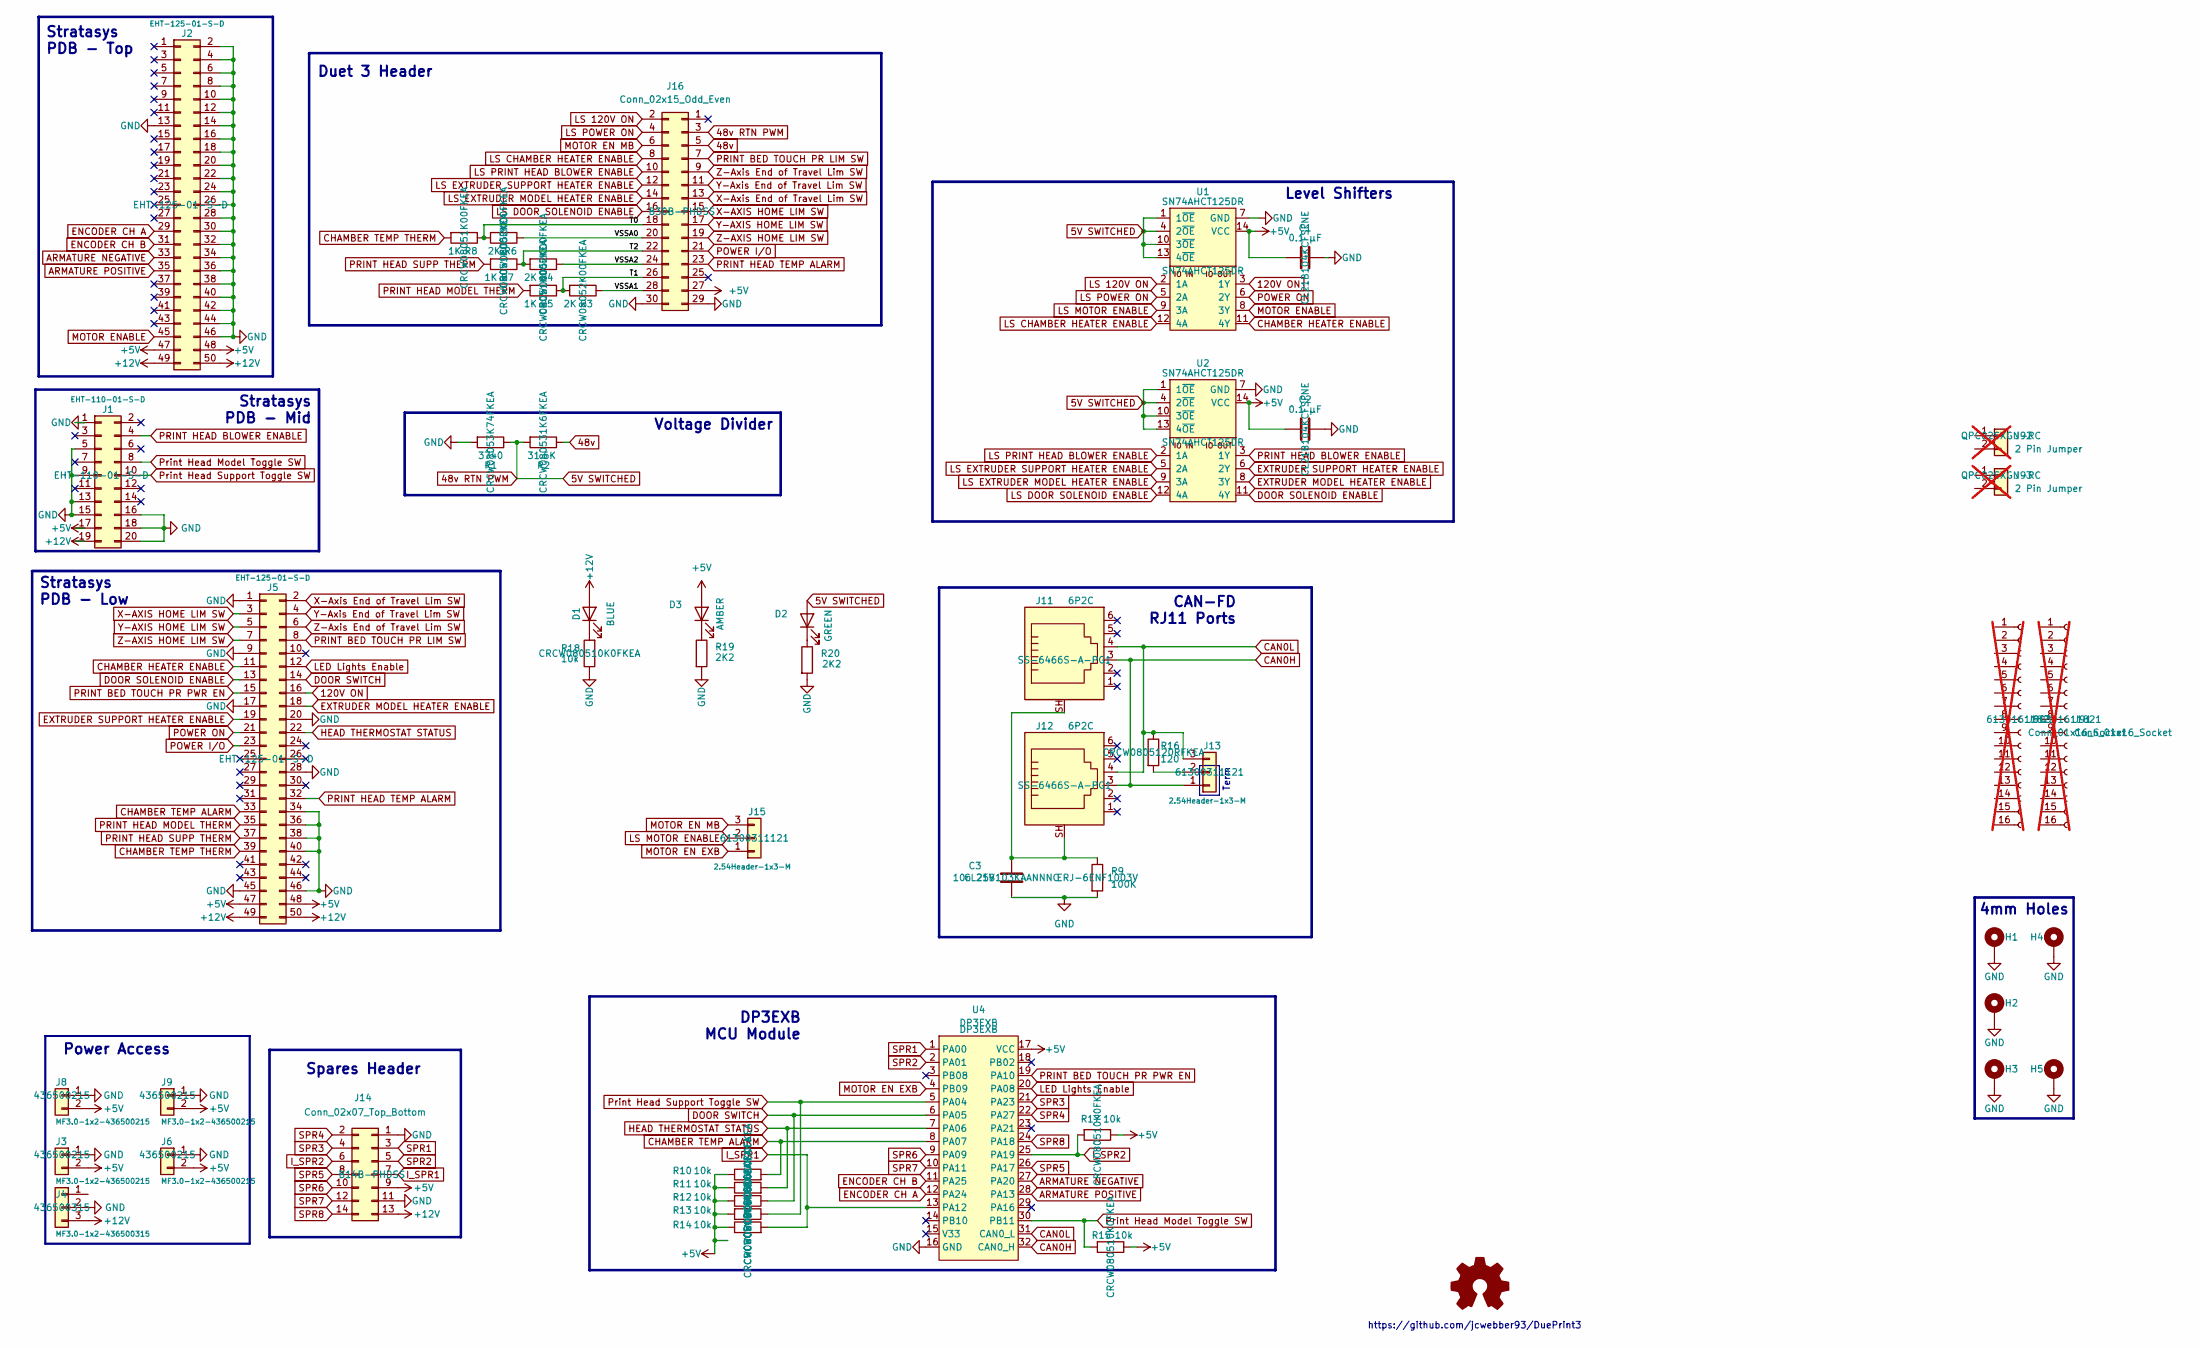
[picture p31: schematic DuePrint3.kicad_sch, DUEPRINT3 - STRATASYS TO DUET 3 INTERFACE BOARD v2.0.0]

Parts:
C1, C2: 0.1 µF; C_0805_2012Metric_Pad1.18x1.45mm_HandSolder; Part Number CL21B104KCFSFNE
C3: 10n 25V; C_0805_2012Metric_Pad1.18x1.45mm_HandSolder; Part Number CL21B103KAANNNC
D1: 12V; LED_0805_2012Metric_Pad1.15x1.40mm_HandSolder; Part Number 150080BS75000
D2: 5V_SW; LED_0805_2012Metric_Pad1.15x1.40mm_HandSolder; Part Number 150080VS75000
D3: 5V; LED_0805_2012Metric_Pad1.15x1.40mm_HandSolder; Part Number 150080AS75000
H1, H2, H3, H4, H5: MountingHole_Pad; MountingHole_4.00mm_Pad
J1: EHT-110-01-S-D; EHT-110-01-XX-D; Part Number EHT-110-01-S-D
J2, J5: EHT-125-01-S-D; SAMTEC_EHT-125-01-S-D; Part Number EHT-125-01-S-D
J3, J6, J8, J9: MF3.0-1x2-436500215; Molex_Micro-Fit_3.0_43650-0215_1x02_P3.00mm_Vertical; Part Number 436500215
J4: MF3.0-1x2-436500315; Molex_Micro-Fit_3.0_43650-0315_1x03_P3.00mm_Vertical; Part Number 436500315
J11, J12: 6P2C; BEL_SS-6466S-A-PG1; Part Number SS-6466S-A-PG1
J13, J15: 2.54Header-1x3-M; PinHeader_1x03_P2.54mm_Vertical; Part Number 61300311121
J14: Conn_02x07_Top_Bottom; JST_PHD_B14B-PHDSS_2x07_P2.00mm_Vertical; Part Number B14B-PHDSS
J16: Conn_02x15_Odd_Even; JST_PHD_B30B-PHDSS_2x15_P2.00mm_Vertical; Part Number B30B-PHDSS
J90, J91: Conn_01x16_Socket; PinHeader_1x16_P2.54mm_Vertical; Part Number 61301611821; not fitted
J92, J93: 2 Pin Jumper; Part Number QPC02SXGN-RC; not fitted
R1: 3740; R_0805_2012Metric_Pad1.20x1.40mm_HandSolder; Part Number CRCW08053K74FKEA
R2: 31.6K; R_0805_2012Metric_Pad1.20x1.40mm_HandSolder; Part Number CRCW080531K6FKEA
R3, R4, R6: 2K; R_0805_2012Metric_Pad1.20x1.40mm_HandSolder; Part Number CRCW08052K00FKEA
R5, R7, R8: 1K; R_0805_2012Metric_Pad1.20x1.40mm_HandSolder; Part Number CRCW08051K00FKEA
R9: 100K; R_0805_2012Metric_Pad1.20x1.40mm_HandSolder; Part Number ERJ-6ENF1003V
R10, R11, R12, R13, R14, R15, R17, R18: 10k; R_0805_2012Metric_Pad1.20x1.40mm_HandSolder; Part Number CRCW080510K0FKEA
R16: 120; R_0805_2012Metric_Pad1.20x1.40mm_HandSolder; Part Number CRCW0805120RFKEA
R19, R20: 2K2; R_0805_2012Metric_Pad1.20x1.40mm_HandSolder; Part Number CRCW08052K20FKEA; LCSC Part # C413087
U1, U2: SN74AHCT125DR; SOIC-14_3.9x8.7mm_P1.27mm; Part Number SN74AHCT125DR
U4: DP3EXB; Part Number DP3EXB

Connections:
48v: J16.5, R2.1
48v RTN PWM: D2.2 (A), J16.3, R1.1, R2.2, U1.1 (1~OE), U1.4 (2~OE), U1.10 (3~OE), U1.13 (4~OE), U2.1 (1~OE), U2.4 (2~OE), U2.10 (3~OE), U2.13 (4~OE)
120V ON: J5.16, U1.3 (1Y)
+5V: C1.1, C2.1, D3.2 (A), J1.17, J2.47, J2.48, J3.2, J5.47, J5.48, J6.2, J8.2, J9.2, J14.9, J16.27, R10.1, R11.1, R12.2, R13.2, R14.1, R15.1, R17.1, U1.14 (VCC), U2.14 (VCC), U4.17 (VCC)
+12V: D1.2 (A), J1.19, J2.49, J2.50, J4.3, J5.49, J5.50, J14.13
/T0: J16.18, R6.2, R8.1
/T1: J16.26, R3.2, R5.1
/T2: J16.22, R4.2, R7.1
/VSSA0: J16.20, R6.1
/VSSA1: J16.28, R3.1
/VSSA2: J16.24, R4.1
ARMATURE NEGATIVE: J2.33, U4.27 (PA20)
ARMATURE POSITIVE: J2.35, U4.28 (PA13)
CAN0H: J11.3, J12.3, J13.1, U4.32 (CAN0_H)
CAN0L: J11.4, J12.4, J13.3, R16.1, U4.31 (CAN0_L)
CHAMBER HEATER ENABLE: J5.11, U1.11 (4Y)
CHAMBER TEMP ALARM: J5.33, R10.2, U4.8 (PA07)
CHAMBER TEMP THERM: J5.39, R8.2
DOOR SOLENOID ENABLE: J5.13, U2.11 (4Y)
DOOR SWITCH: J5.14, R12.1, U4.6 (PA05)
ENCODER CH A: J2.29, U4.12 (PA24)
ENCODER CH B: J2.31, U4.11 (PA25)
EXTRUDER MODEL HEATER ENABLE: J5.18, U2.8 (3Y)
EXTRUDER SUPPORT HEATER ENABLE: J5.19, U2.6 (2Y)
GND: C1.2, C2.2, C3.2, H1.1, H2.1, H3.1, H4.1, H5.1, J1.1, J1.5, J1.9, J1.13, J1.15, J1.16, J1.18, J1.20, J2.2, J2.4, J2.6, J2.8, J2.10, J2.12, J2.13, J2.14, J2.16, J2.18, J2.20, J2.22, J2.24, J2.26, J2.28, J2.30, J2.32, J2.34, J2.36, J2.38, J2.40, J2.42, J2.44, J2.46, J3.1, J4.2, J5.1, J5.9, J5.17, J5.20, J5.28, J5.34, J5.36, J5.38, J5.40, J5.45, J5.46, J6.1, J8.1, J9.1, J14.1, J14.11, J16.29, J16.30, R1.2, R9.2, R18.1, R19.2, R20.2, U1.7 (GND), U2.7 (GND), U4.16 (GND)
HEAD THERMOSTAT STATUS: J5.22, R11.2, U4.7 (PA06)
I_SPR1: J14.7, R14.2, U4.13 (PA12)
I_SPR2: J14.6, R17.2, U4.25 (PA19)
LED Lights Enable: J5.12, U4.20 (PA08)
LS 120V ON: J16.2, U1.2 (1A)
LS CHAMBER HEATER ENABLE: J16.8, U1.12 (4A)
LS DOOR SOLENOID ENABLE: J16.16, U2.12 (4A)
LS EXTRUDER MODEL HEATER ENABLE: J16.14, U2.9 (3A)
LS EXTRUDER SUPPORT HEATER ENABLE: J16.12, U2.5 (2A)
LS MOTOR ENABLE: J15.2, U1.9 (3A)
LS POWER ON: J16.4, U1.5 (2A)
LS PRINT HEAD BLOWER ENABLE: J16.10, U2.2 (1A)
MOTOR EN EXB: J15.1, U4.4 (PB09)
MOTOR EN MB: J15.3, J16.6
MOTOR ENABLE: J2.45, U1.8 (3Y)
unnamed: C3.1, J11.SH, J12.SH, R9.1
unnamed: D1.1 (K), R18.2
unnamed: D2.1 (K), R20.1
unnamed: D3.1 (K), R19.1
unnamed: J13.2, R16.2
POWER I/O: J5.23, J16.21
POWER ON: J5.21, U1.6 (2Y)
PRINT BED TOUCH PR LIM SW: J5.8, J16.7
PRINT BED TOUCH PR PWR EN: J5.15, U4.19 (PA10)
PRINT HEAD BLOWER ENABLE: J1.4, U2.3 (1Y)
PRINT HEAD MODEL THERM: J5.35, R5.2
PRINT HEAD SUPP THERM: J5.37, R7.2
PRINT HEAD TEMP ALARM: J5.32, J16.23
Print Head Model Toggle SW: J1.8, R15.2, U4.30 (PB11)
Print Head Support Toggle SW: J1.10, R13.1, U4.5 (PA04)
SPR1: J14.3, U4.1 (PA00)
SPR2: J14.5, U4.2 (PA01)
SPR3: J14.4, U4.21 (PA23)
SPR4: J14.2, U4.22 (PA27)
SPR5: J14.8, U4.26 (PA17)
SPR6: J14.10, U4.9 (PA09)
SPR7: J14.12, U4.10 (PA11)
SPR8: J14.14, U4.24 (PA18)
X-AXIS HOME LIM SW: J5.3, J16.15
X-Axis End of Travel Lim SW: J5.2, J16.13
Y-AXIS HOME LIM SW: J5.5, J16.17
Y-Axis End of Travel Lim SW: J5.4, J16.11
Z-AXIS HOME LIM SW: J5.7, J16.19
Z-Axis End of Travel Lim SW: J5.6, J16.9

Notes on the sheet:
Duet 3 Header
4mm Holes
Stratasys PDB - Mid
CAN-FD RJ11 Ports
Level Shifters
Stratasys PDB - Low
Stratasys PDB - Top
https://github.com/jcwebber93/DuePrint3
Spares Header
Term
Voltage Divider
DP3EXB MCU Module
Power Access

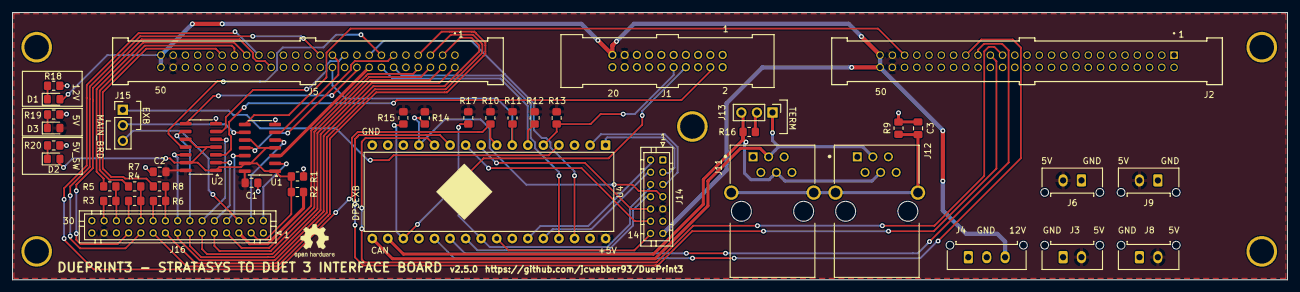
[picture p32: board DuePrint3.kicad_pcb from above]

Board: 2 copper layers, 208.2 x 43.6 mm, 48 parts (0 on the bottom side), 69 nets.

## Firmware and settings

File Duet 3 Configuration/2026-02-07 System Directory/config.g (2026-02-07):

; Enable network
if {network.interfaces[0].type = "ethernet"}
    M552 P0.0.0.0 S1			; enable DHCP for ethernet
else
    M552 I1 S1

M552 I1 S1                            ; enable wifi

G4 S5                                 ;wait for expansion boards to start
M550 P"DuePrint3 BST 1200es"

; Drives
M569 P0 S1                            ;physical drive 0 goes backwards, X-Axis
M569 P1 S0                            ;physical drive 1 goes forwards, Y-Axis
M569 P2 S1                            ;physical drive 2 goes forwards, Z-Axis
M569 P124.0 S0 T0:0:0:0               ;external driver on sammy 12/7 latest
M584 X0 Y1 Z2 E124.0                  ;set drive mapping
M350 X16 Y16 Z16 E16 I1               ;configure microstepping with interpolation
M92 X53.33 Y134 Z629.864 E323.08     ;set steps per mm was 1011.99 then 1594.6, then 642.61
M566 X400 Y400 Z30 E3000              ;set jerk E was 60, x and y was 600
M203 X30000 Y18000 Z1200 E2700.00      ;set max speeds (mm/min)
M201 X2000 Y2000 Z1000 E3000            ;set max accelerations (mm/s^2) X and Y were both 2500 and 3500 E was 2000
M201.1 X750 Y750 Z2000 E3000            ;max special acceleration move (homing)
M906 X1800 Y2600 Z2600 I30            ;set motor currents (mA) and motor idle percent
M84 S30                               ;set idle timeout

M208 X-138.3 Y-137.5 Z-2 S1           ;set axis minima
M208 X160.4 Y182 Z325.2 S0              ;set axis maxima
; Toggle nozzle min - -163.2 , 184.6 max
; X EOT toggles at 160.5
; Y EOT at 182.5
; Z High (bottom) at 325.5, low EOT at -4.6
;purge bucket near middle - x162.5, y155.5

;z probe left toggle -136.5
;z probe right toggle 197.5

;Z bottom (EOT) 325.1



;Endstops

M574 X1 S1 P"!io0.in"                 ; X home limit (low side)
M574 Y1 S1 P"!io1.in"                 ; Y home limit (low side, toward front of printer
M574 Z2 S1 P"!io6.in"                   ; assign Z EOT to x endstop on high side


; Z-Probe
M558 P5 H5 F1200:200 T18000 A3 C"!io2.in" ; Z probe, set dive height, probe speed and travel speed
;G31 P1000 X-46 Y-74 Z0.896
;G31 P1000 X-24 Y-73 Z1.365
;G31 P1000 X24 Y73 Z1.9                    ;Increase value to bring it closer to the bed, decrease to move it away
G31 P1000 X24 Y73 Z2.1                    ;Increase value to bring it closer to the bed, decrease to move it away UPDATED 01/04 
;G31 P1000 X24 Y96 Z0.896                          ; set Z probe trigger value, offset and trigger height
;M557 X-135:135 Y-135:65 P5:5          ; define mesh grid. The whole bead cannot be probed due to the position of the probe.
;M557 X-134:140 Y-127:146.82 P3:3          ; define mesh grid. The whole bead cannot be probed due to the position of the probe. Changed 11/15/2025
M557 X-134:140 Y-127:140 P3:3          ; define mesh grid. The whole bead cannot be probed due to the position of the probe.

; Head Blower Fan
M950 P0 C"io2.out"
M42 P0 S0                             ; enable blower

; Extruder Motor Enable
M950 P1 C"io3.out"
M42 P1 S0

; Touch Power Enable
M950 P2 C"124.pa25"
M42 P2 S0

; Door Enable
M950 P3 C"io6.out"
M42 P3 S0

; LED Lights Enable
M950 P4 C"124.pa24"
M42 P4 S0                             ;S1 to turn on!

; 120v ON
M950 P5 C"io0.out"
M42 P5 S0                   ; LETS START WITH S0 TO BE OFF?

; CONTROLLED POWER SHUTDOWN ENABLE
M950 P6 C"io1.out"
M42 P6 S0                   ; LETS START WITH S0 TO BE OFF?

; DISABLE OUTPUTS
M950 P7 C"!out4"
M42 P7 S1                   ; S1 OUTPUTS DISABLED


; Thermocouples
M308 S0 A"Chamber Test" P"temp0" Y"linear-analog" F0 B-42 C113
M308 S1 A"Model Test" P"temp1" Y"linear-analog" F0 B12.5 C328
M308 S2 A"Support Test" P"temp2" Y"linear-analog" F0 B12.5 C328

; Heaters
M140 H-1                              ;Disable bed heater
M950 H0 C"io4.out" T0                   ; chamber, sensor 0
M141 H0                               ; map chamber to heater 0
M143 H0 S85                           ; set temperature limit for heater 0 to 85C
M570 H0 P60 T10                       ; Increase fault delay to 30s, decrease temperature fault to 10c
M950 H1 C"io5.out" T1                   ; model, sensor 1
M143 H1 S320
M570 H1 P30                           ; set fault time delay to 30s for heater 1
M950 H2 C"io7.out" T2                   ; support, sensor 2
M143 H2 S320                          ; set temperature limit for heater 1 to 320C
M570 H2 P30                           ; set fault time delay to 30s for heater 2

; Tools
M563 P0 S"Model" D0 H1                ; define tool 0
G10 P0 X0 Y0 Z0                       ; set tool 0 axis offsets
G10 P0 R0 S0                          ; set initial tool 0 active and standby temperatures

M563 P1 S"Support" D0 H2              ; define tool 1
G10 P1 X-20.3 Y0 Z-0.025                    ; set tool 1 axis offsets
G10 P1 R0 S0                          ; set initial tool 1 active and standby temperatures

; Head Thermostat Status
M950 J1 C"124.pa06"

; Door In
M950 J2 C"124.pa05"

; Print Head Support Toggle
M950 J3 C"124.pa04"

; Print Head Model Toggle
M950 J4 C"124.pb08"

; X-axis EOT
M950 J5 C"!io3.in"

; Y-axis EOT
M950 J6 C"!io4.in"

; Z-axis Home
M950 J7 C"!io5.in"

; Z-axis EOT
;M950 J8 C"!io6.in"

; Print Head Temp Alarm
M950 J9 C"!io7.in"

; Chamber Temp Alarm
M950 J10 C"124.pa07"

;POWER SWITCH
M950 J11 C"io8.in"

M955 P120.0 I01
M501                                  ;config g
M302 S280 R280
M572 D0 S.065
M593 P"zvdd" F43
M207 P0 S0.35 Z.35 F2700
M207 P1 S0.35 Z.35 F2700
M98 P"globals.g"
M98 P"/macros/startup.g"
M912 P0 S-14

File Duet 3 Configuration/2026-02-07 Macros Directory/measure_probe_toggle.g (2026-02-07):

if !move.axes[0].homed || !move.axes[1].homed	        ; If the printer hasn't been homed, home it
	G28 XY	                                             ; home X, Y. Z will be homed if its not during X homing script

M564 S0 ; Allow movement beyond printer limits
G1 X-100 Y178.5 F18000; Move to back of Printer

G91     ;relative positioning

var deploy_trigger = 0
M558 P5 C"nil"						;Unassign Z-Probe
M574 X1 S1 P"io2.in"                 ; X home limit (low side) note that the input is not inverted for this measurement!
G1 H4 X-150 F1800
set var.deploy_trigger = move.axes[0].machinePosition
;M574 X1 S1 P"!io0.in" ;reassign original x home

var retract_trigger = 0
M574 X2 S1 P"!io2.in" 		; assign X EOT to x endstop on high side, invert input
G1 H4 X500 F1800
set var.retract_trigger = move.axes[0].machinePosition
M574 X1 S1 P"!io0.in" ;reassign old x home
M558 P5 C"!io2.in" ; Z probe, set dive height, probe speed and travel speed

G90

M98 P"/macros/purgepark.g"
M564 S1			;Restrict movement to axis limits

echo "Deploy Position:" ^ var.deploy_trigger ^ ", Retract Position:" ^ var.retract_trigger
T-1

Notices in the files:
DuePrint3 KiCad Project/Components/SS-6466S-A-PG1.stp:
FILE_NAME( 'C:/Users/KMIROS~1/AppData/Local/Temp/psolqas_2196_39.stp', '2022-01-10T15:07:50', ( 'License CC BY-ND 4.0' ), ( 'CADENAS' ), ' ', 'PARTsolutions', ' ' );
